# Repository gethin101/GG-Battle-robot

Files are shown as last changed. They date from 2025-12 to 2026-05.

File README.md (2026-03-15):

# Gethin's Custom BATTLE ROBOT
**This is my custom Robot Wars inspired battle robot with a servo-driven axe weapon, wireless radio frequency remote control, LCD display, RGB lights, and audio sound effects. My robot is controlled by a custom PCB RF remote using a Raspberry Pi Pico H microcontroller running CircuitPython and the chassis and axe will be 3D printed in PLA.**

It runs on a Raspberry pi pico H, TT motors, L298N motor drivers, and a servo motor. It is controlled by a 433mhz radio frequency remote, another Raspberry pi pico H, a joystick module and extra control buttons. The 2 main axe weapons and chassis will be 3d printed in PLA.

I am also using a 1.8" SPI LCD Display for the robot to display information on the front of the robot and SK6812 MINI-E RGB leds for the back of the robot. These will both be powered by being plugged into the breadboard in the robot using the pins and jumper wires.

Also I have sound effects for my robot. I will do this through a PAM8302 amplifier board and 8Ω 2W speaker. The amplifier board will go into the breadboard & the speaker will plug directly into the PAM8302.

**It is powered by AA batteries, the actual robot will be connected using a breadboard & jumper wires, but I wanted to create a custom PCB for my remote. I designed the PCB in KiCad, also with female sockets so I can remove modules from the remote.**

**Note:** I had to connect the grounds on either side together so they have the same voltage reference point.

My weapon system consists of a servo motor embedded on the underside of the top half of the chassis that will swing the PLA axe weapon down to hit, and back up to rest on the slanted design of the robot.

---

## Inspiration
I wanted to make this project to help me learn CAD design through Fusion 360, PCB design in KiCad and get me into the world of electronics and embedded systems.
I designed my robot with inspiration from Thor in Robot Wars with the axe weapon idea and Apollo with the general shape and aesthetics

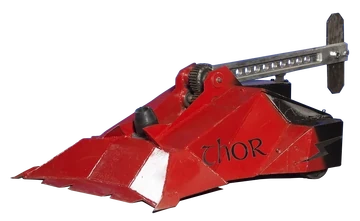
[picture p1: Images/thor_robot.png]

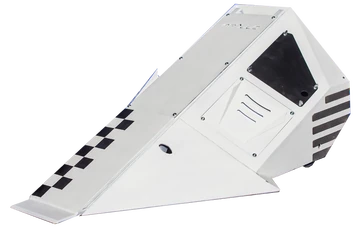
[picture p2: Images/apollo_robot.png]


---

## Control

I control my robot through the use of the PCB remote. There is a joystick module that with the use of the RF transmitter, will control the TT motors on the robot and therefore the movement of the wheels. 

I have also added a button on the remote to control the servo motor that moves the PLA axe weapon and also a few buttons that play sound effects and display custom data on the display.

---

## **Remote PCB:**

**Solder:**
- Battery wires to copper pad
- Pico through hole
- Buttons

**Headers:**
- RF module
- Joystick
- Boost converter

Remote PCB design:

**This was my first PCB design before I made it in KiCad**

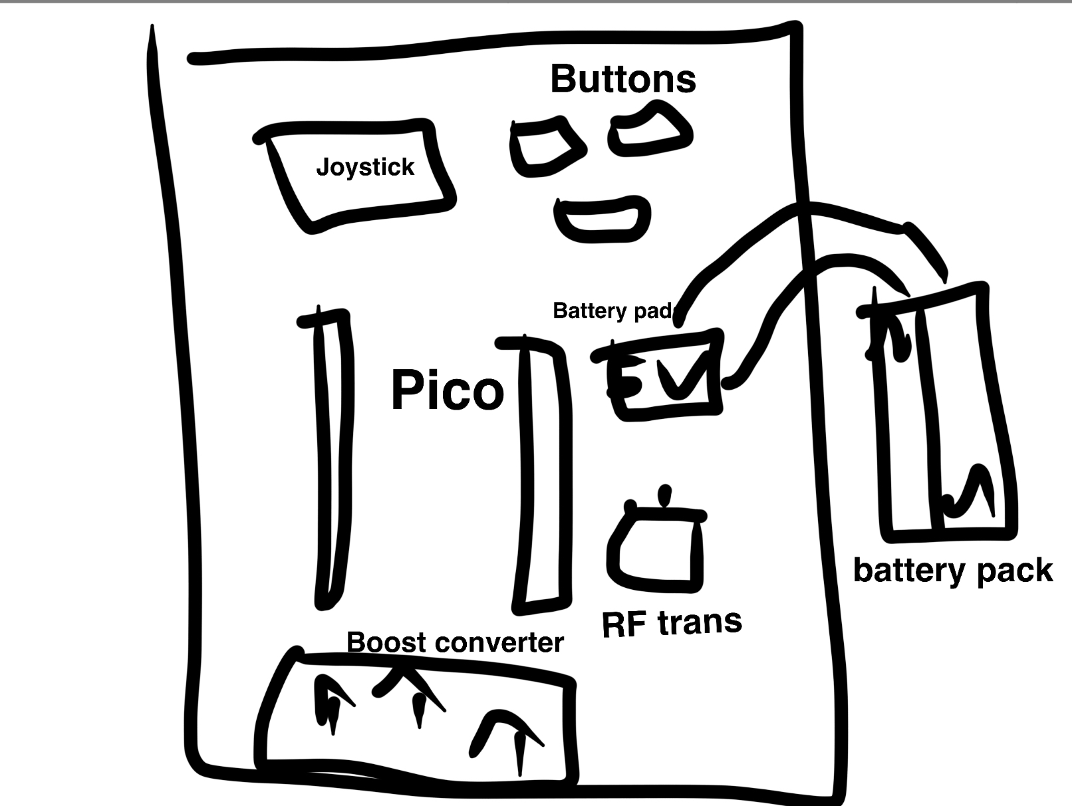
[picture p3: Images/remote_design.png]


I then designed my remote PCB in KiCad with the schematic below showing how all the components are connected:

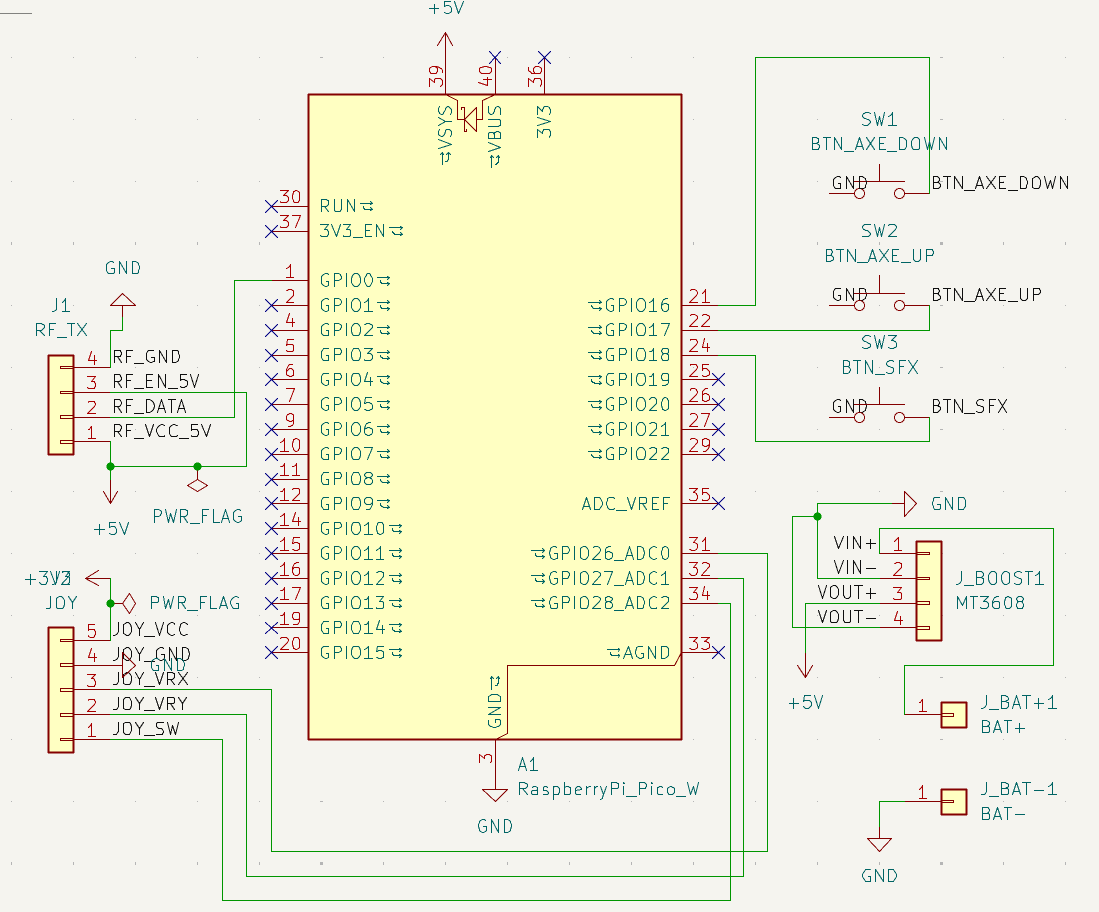
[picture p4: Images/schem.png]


**PCB design process:**

I designed my remote PCB in KiCad. I made through-hole pins for the pico where I will have the choice to either solder on female headers which will allow easy removal of the pico for the remote or to directly solder them on. 
This took some time to design as I wasn't sure on which approach would better fit my project, so I left it for my decision when I get the parts.

Next, I added 3 small buttons that I will solder straight onto the PCB. These will be used as control buttons for the robot where I will program them to sent certains signals to the robot, for example to move the axe head up or down with the servo motor, or to carry out pre-programmed movement plans with the TT motors and wheels.

I added two copper pads for the battery+ and battery- to my PCB to power the remote and I ended up decising to put these on the back side of the PCB so it leaves more space on the front and so I can more easily secure the battery pack on the rear side of the remote, with plently of space to move it around before deciding the final position.

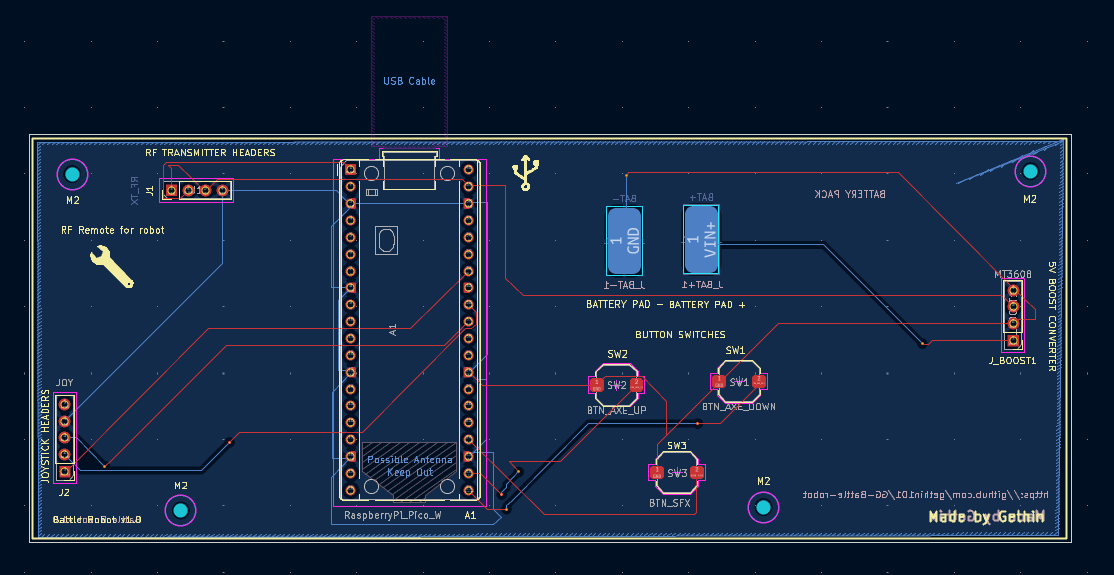
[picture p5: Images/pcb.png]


I added holes in my PCB where I will solder on female header pins for the radio frequency transmitter device so it can be easily removed if I come across any issues. I repeated this process on different parts of the remote for the joystick device and 5V boost converter to allow for efficient and easy assembly once I'm ready to build my robot. I first went for through-hole pins in my original design but altered it to have header pins as it will be easier to assemble and tinker with.

Next, I added some silkscreen details onto my PCB such as my name, GitHub repo link and a small mechanical logo. This added a bit more personality to my remote and will allow for it to be easier to distinguish from other robots (ik this is only the remote and will most likely be covered later on, but it was fun to mess about with)

I learnt how to add drill holes on the corners of my PCB so it has the option to be secured into a case and therefore will be more comfortable to use with nothing moving about. Furthermore, I also learnt how to make a copper GND pour which I have found out reduces noise on the PCB and allowed me to have better accessibility to the GND on the remote when I was designing and wiring it in KiCad.

I am happy with my remote PCB and I ran the ERC and DRC checkers a few times, fixed all the issues and now it comes up with no errors when I run them.

The KiCad project files & gerber.zip are both in **PCB/** and the PCB cart screenshot from JLCPCB is below

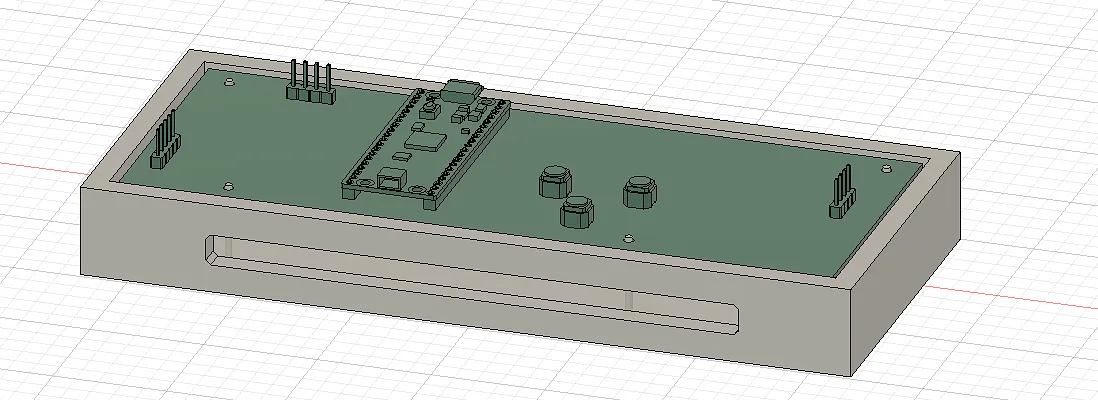
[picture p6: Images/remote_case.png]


---

## Cart Screenshots

**Here are the cart screenshots for all of my components. I have logged the prices exactly, but there are some discounts and sales on atm that are ending soon so it may end up costing a bit more.**

<details>
<summary>Click to see cart screenshots</summary>
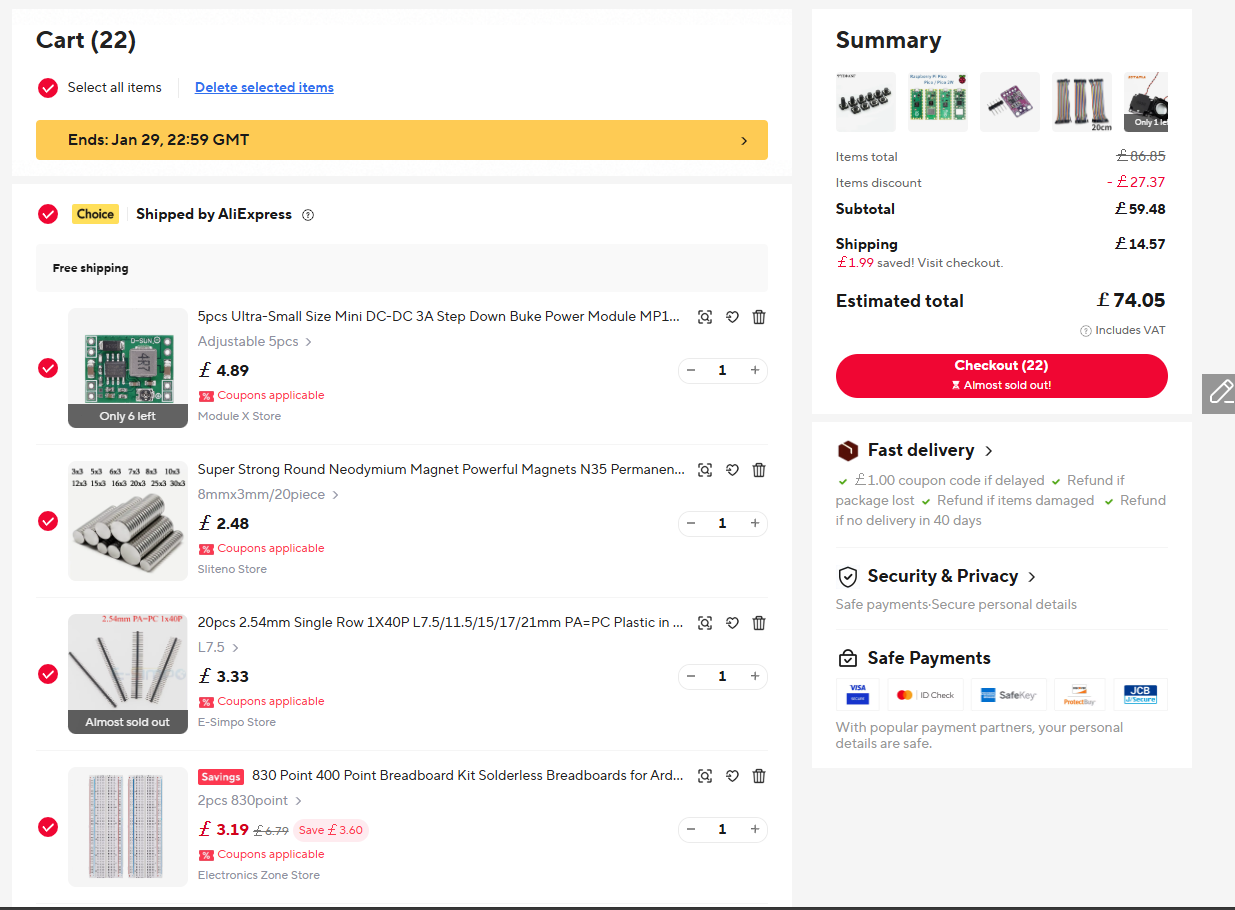
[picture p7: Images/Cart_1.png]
cart screenshot


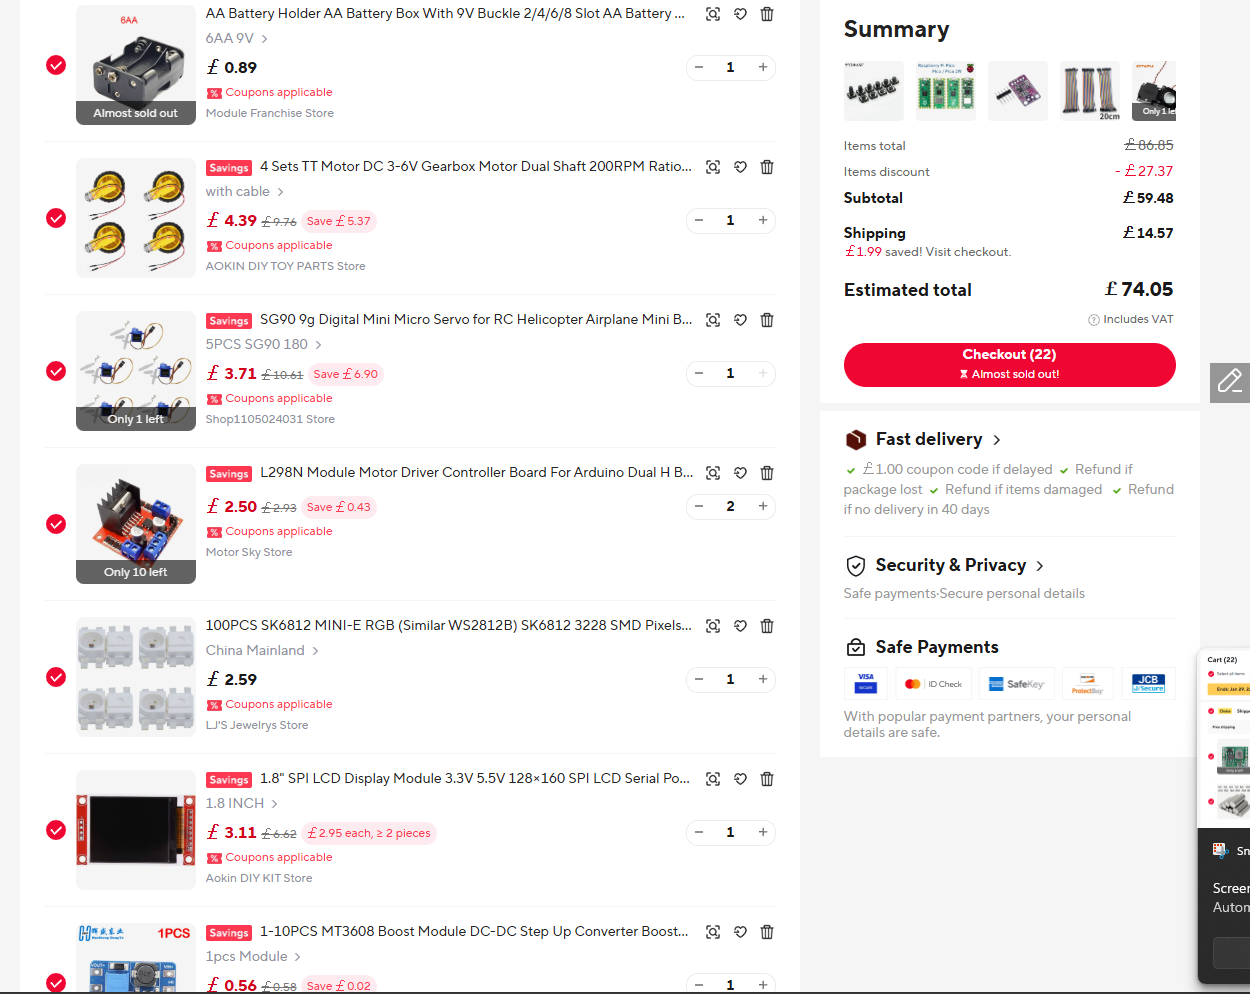
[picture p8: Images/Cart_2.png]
cart screenshot


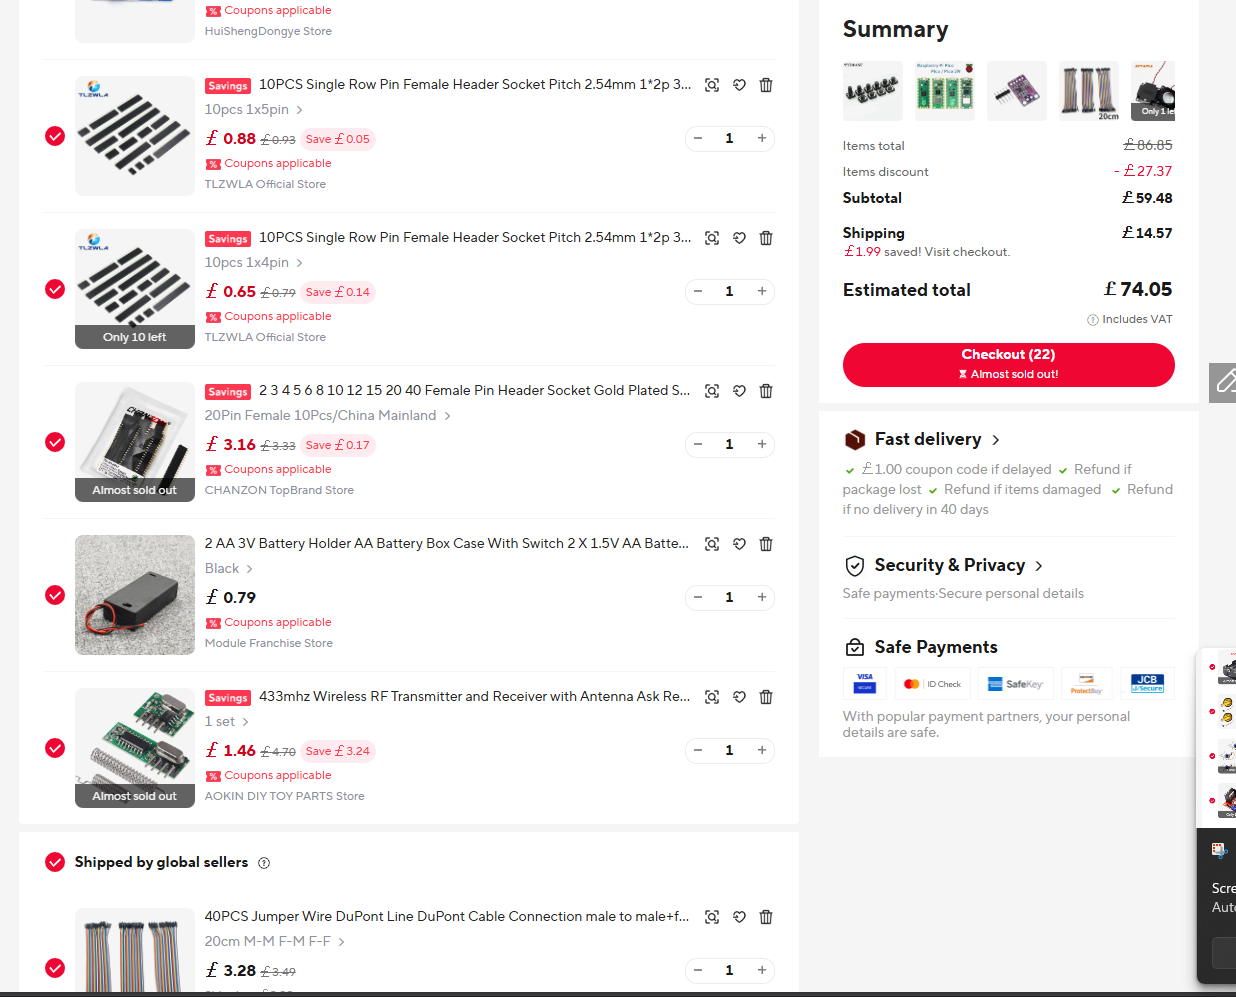
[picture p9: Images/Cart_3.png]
cart screenshot


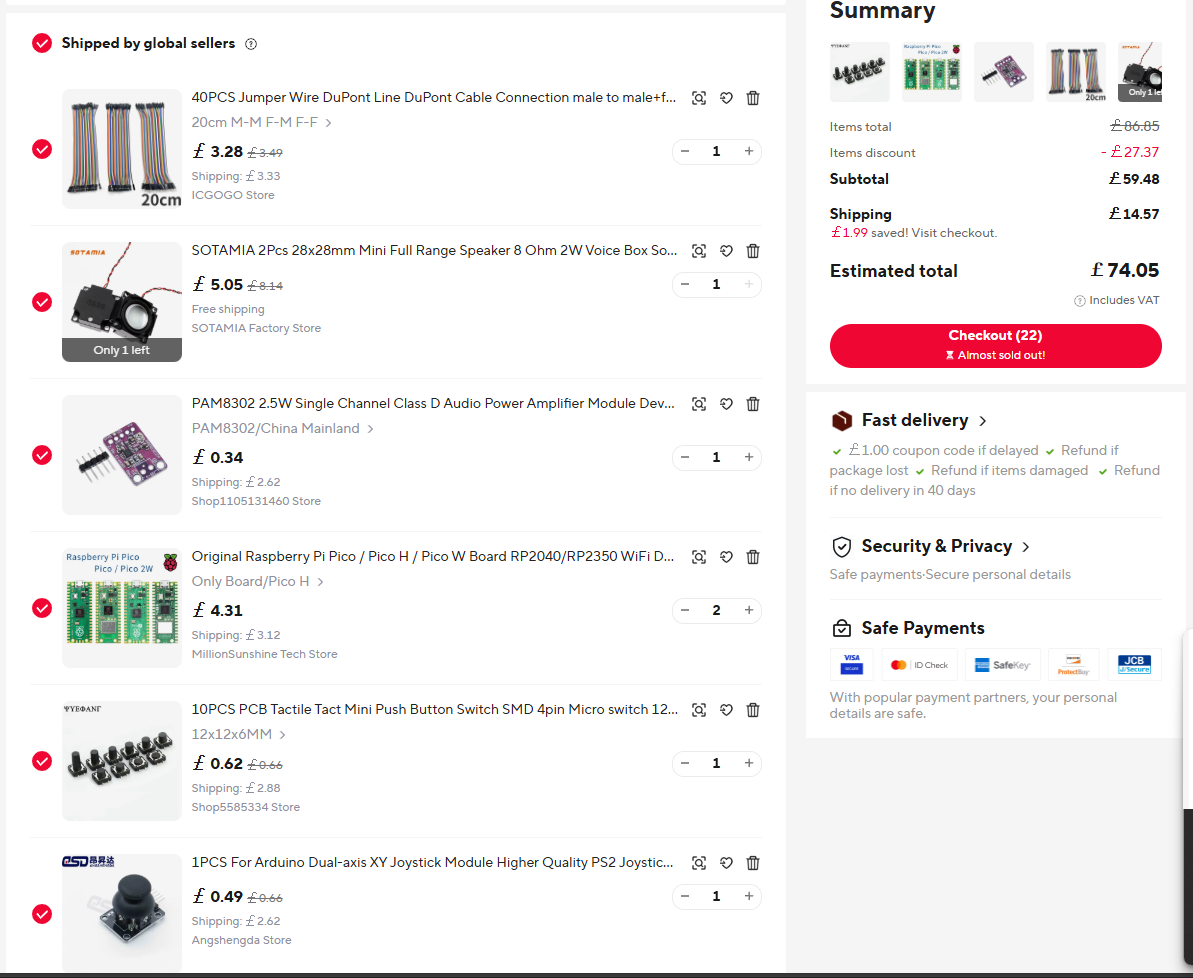
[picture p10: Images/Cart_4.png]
cart screenshot


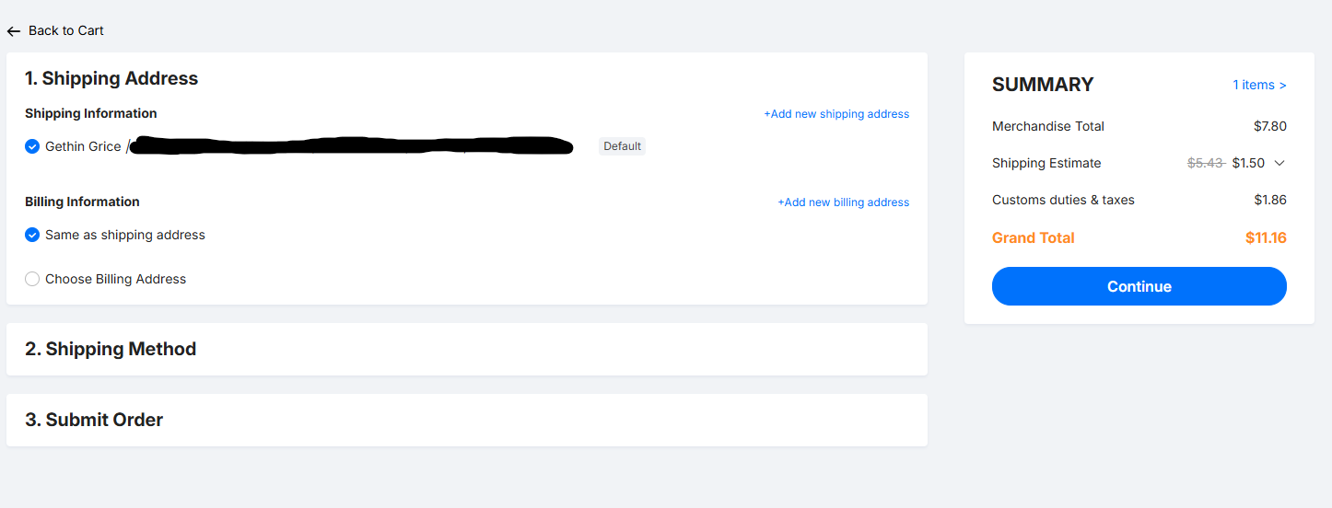
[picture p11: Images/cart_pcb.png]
cart screenshot

</details>

---

## Components

Here are the lists of components for my robot. I have also made a [full BOM](BOM.md)
with links to all the parts.

**List of components for remote:**

- Raspberry pi pico H
- Joystick module
- 433 MHz transmitter
- 2xAA Battery pack
- Custom PCB for joystick, transmitter, microcontroller, battery input & boost converter
- A few buttons for display, audio & specific movement plans
- Female sockets for component removal
- 5V boost converter

**List of components for robot:**

- Raspberry pi pico H
- 1.8" SPI LCD Display
- SK6812 MINI-E RGBs
- PAM8302 amplifier board
- 8Ω 2W speaker
- 433 MHz receiver
- 2x L298N motor drivers
- 4x TT motors (raw voltage from L298Ns)
- Servo motor
- 6xAA battery pack
- Breadboard
- Jumper wires for wiring
- PLA axe
- 3D printed chassis
- 5V buck converter
- Magnets for top & bottom chassis connection

**My project should cost around $104 so should be tier 2**

---
This was my first hand sketch of the component positioning in my robot but obviously I've changed bits of it

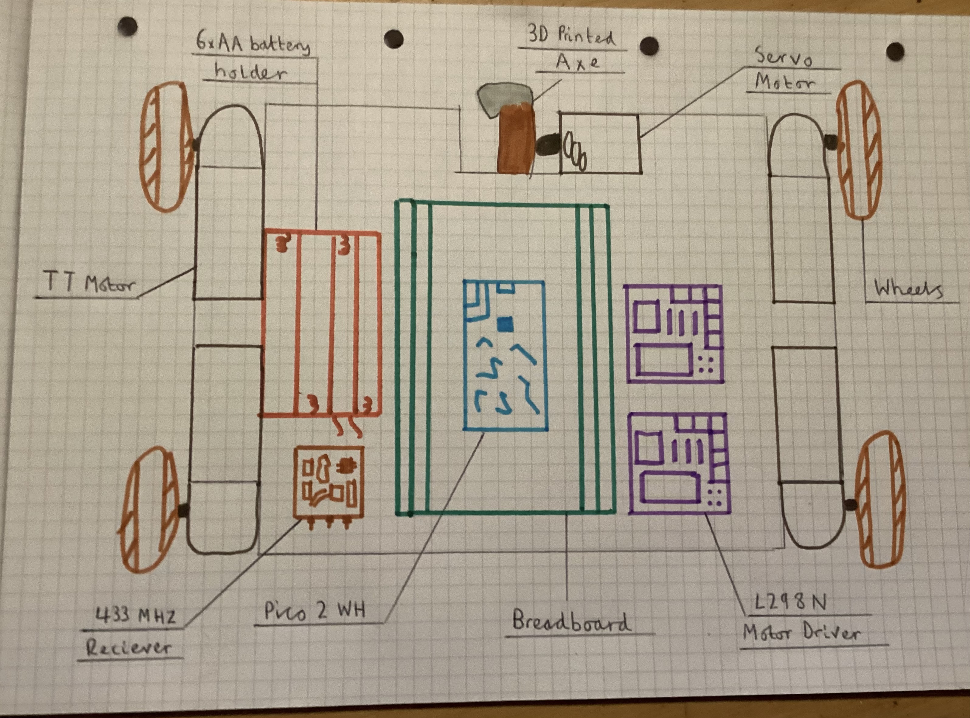
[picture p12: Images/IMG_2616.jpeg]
original wiring diagram


This is a (bit messy) wiring diagram for the robot breadboard system

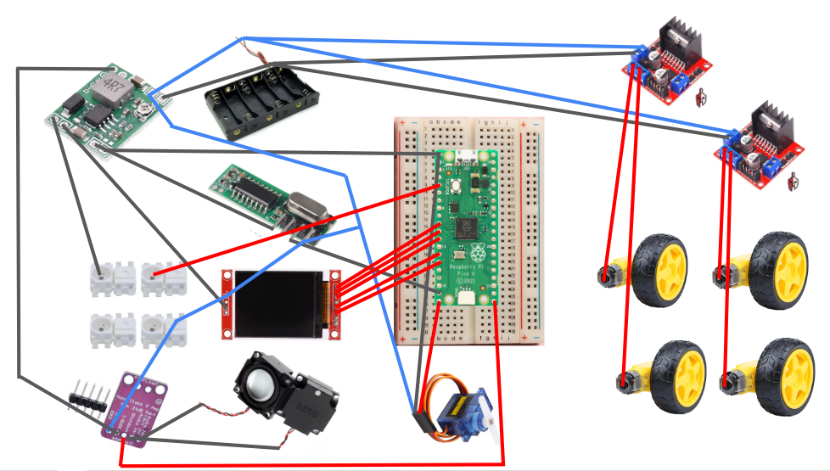
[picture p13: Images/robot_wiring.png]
wiring diagram robot


---

First 3D fusion model of robot chassis:

I originally designed it like this with 2 axe weapons and patterns but have changed to the version below instead.

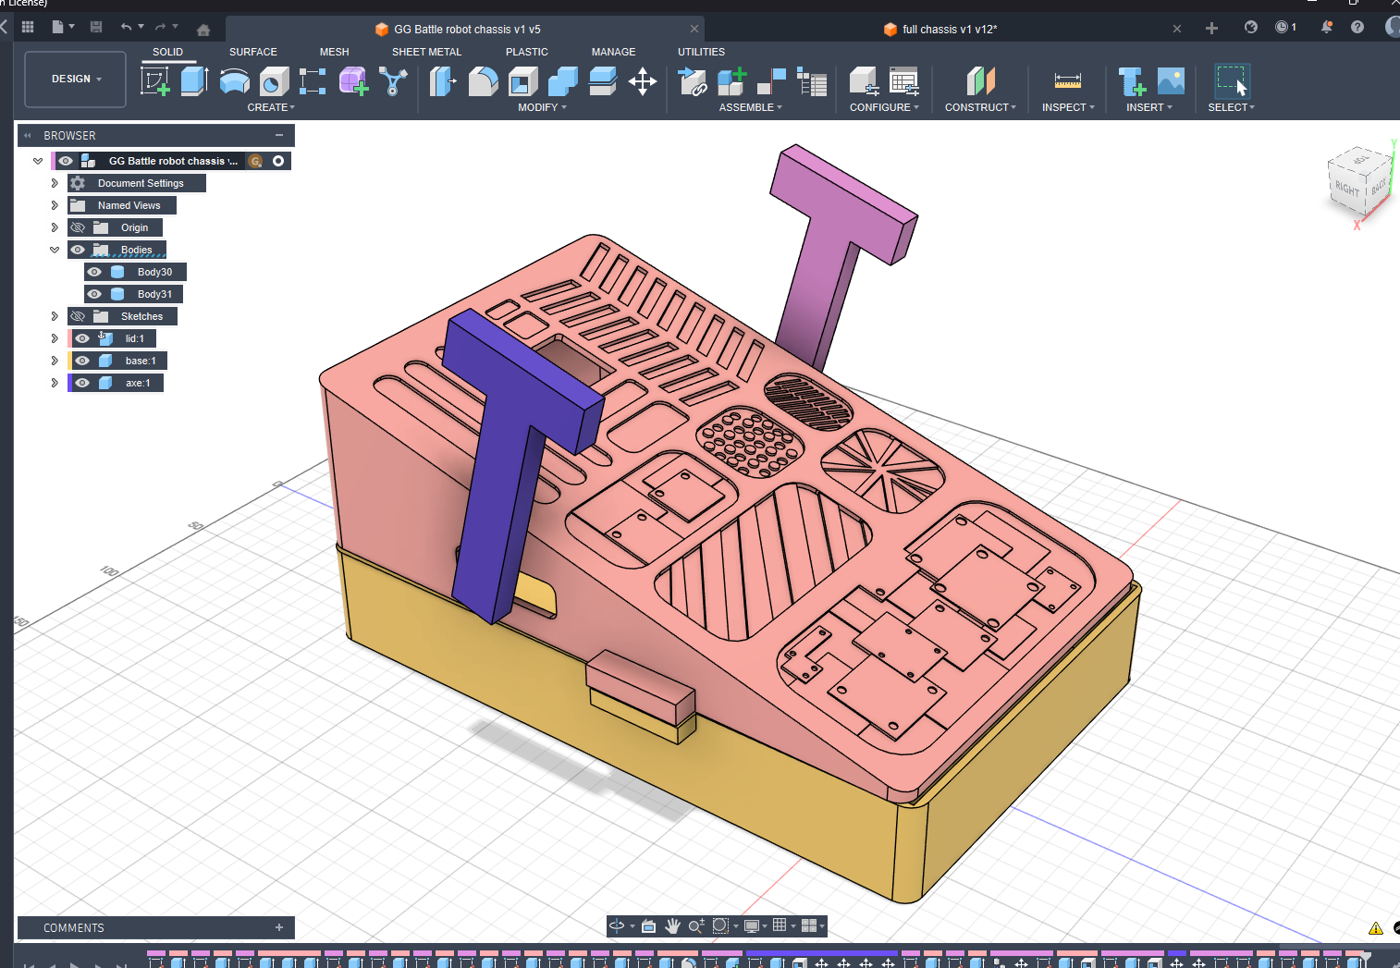
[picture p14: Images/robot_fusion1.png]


This version is the final concept for my robot chassis

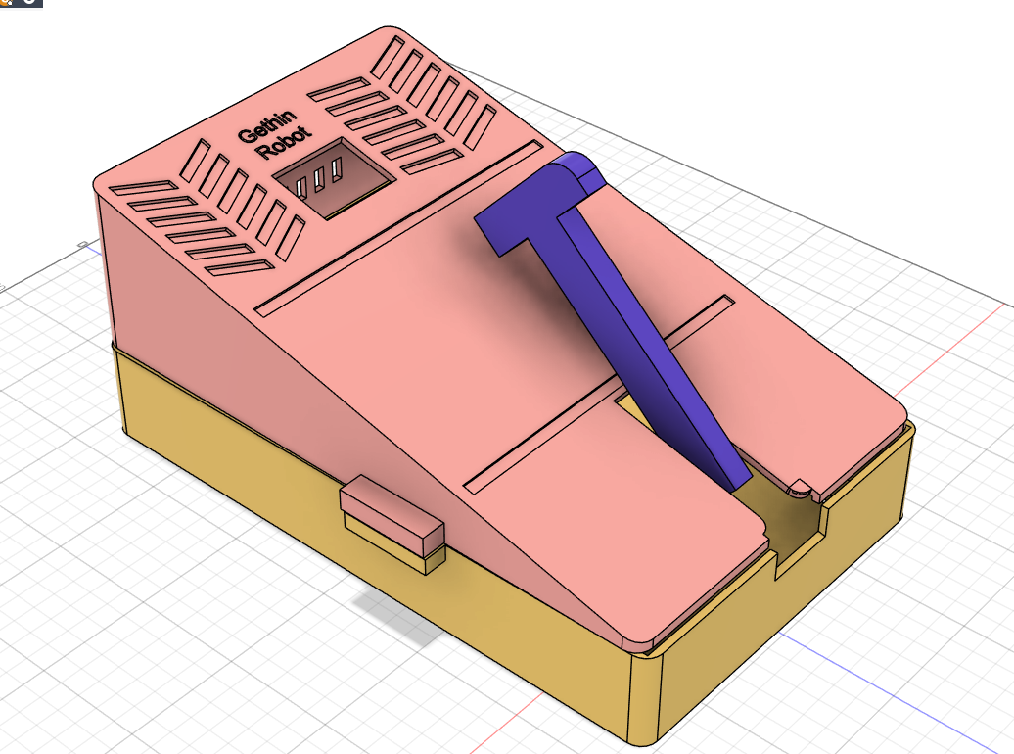
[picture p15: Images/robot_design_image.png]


Rendered robot with textures applied & motors & wheels components

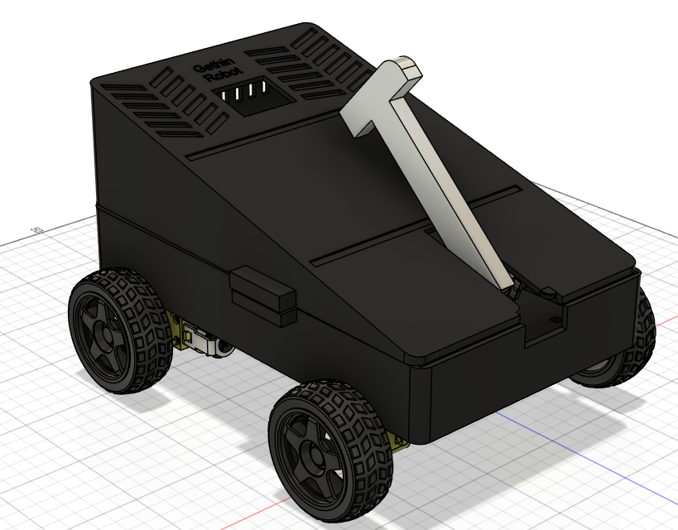
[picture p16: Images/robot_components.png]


Showing servo motor setup with axe and TT motors

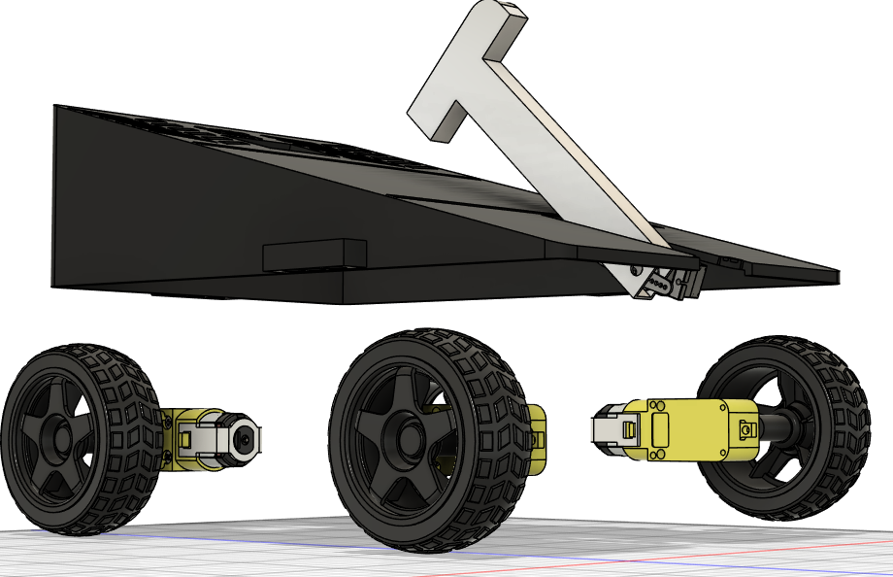
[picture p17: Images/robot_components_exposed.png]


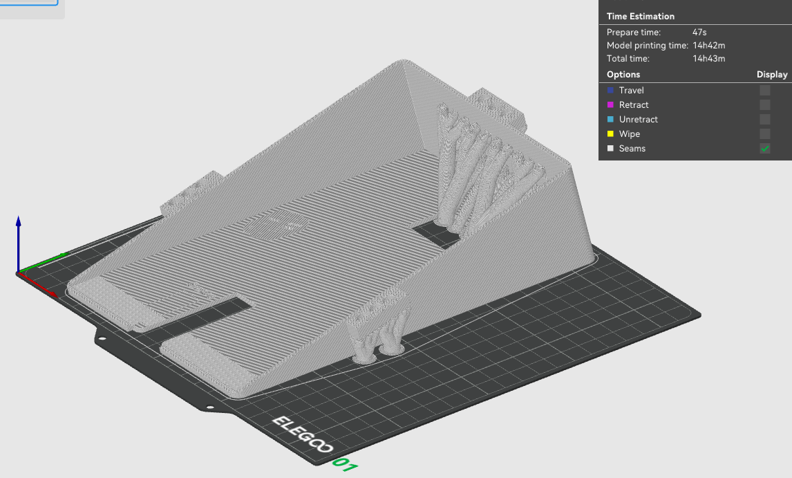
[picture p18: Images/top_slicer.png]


Base bottom of the robot without top half of the chassis

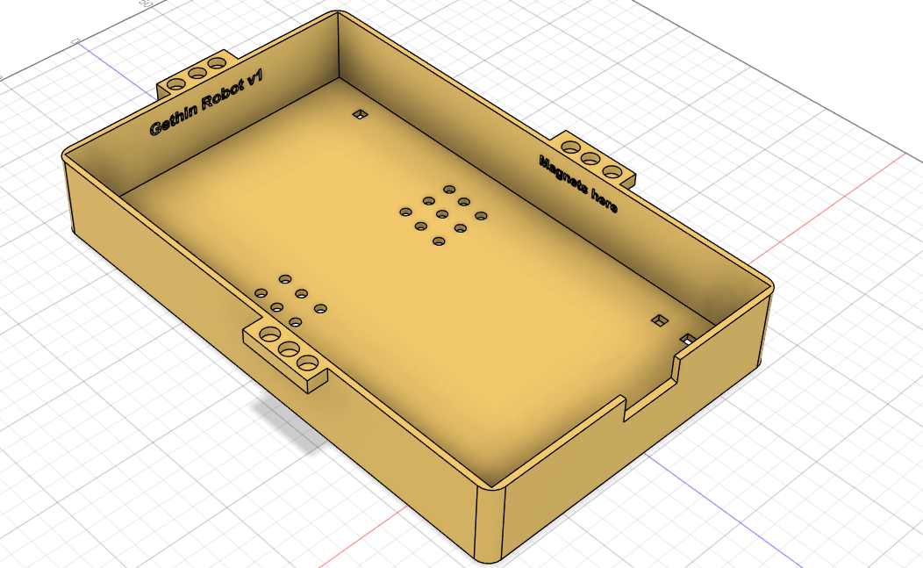
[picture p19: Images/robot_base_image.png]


---
# BOM

**Please note that I am requesting $100 and I will pay for the rest myself**

See [BOM](/BOM.csv)

---
**I will make different iterations and designs for the chassis another time but this is my first design for blueprint**

---

## CircuitPython firmware

- I will need to flash [CircuitPython](/Firmware/adafruit-circuitpython-raspberry_pi_pico2-en_GB-10.1.3.uf2) onto my picos
- Install circuitpython libraries .mpys
- Upload the different [code.pys](Firmware/) to my picos
- Test the firmwares are working

# Blueprint requirements

- [✅] A short description of what your project is  
- [✅] A couple of sentences on how to use your project  
- [✅] A couple of sentences on why you made the project  

- [✅ ] Screenshot of a full 3D model of your project  
- [✅ ] Screenshot of your PCB (if applicable)  
- [✅ ] Wiring diagram (if any wiring is not on a PCB)  
- [✅] Bill of Materials (BOM) in table format at the end of the README, with links [BOM](/BOM.csv)

- [✅] Fully original, customized design (not a direct copy of any guide)  
- [✅] Complete CAD assembly including all components (electronics included)  
- [✅] Firmware present (even if untested)  
- [✅] Design sanity‑checked with someone else  approved by [@LoganPeterson](https://hackclub.enterprise.slack.com/team/U079WLY0HLY)

- [✅] BOM in CSV format in the root directory, with links
- [✅] PCB source files (.kicad_pro, .kicad_sch, gerbers.zip, etc.) if applicable  
- [✅] A .STEP file of the full 3D CAD model including electronics  
- [✅] Source CAD files (.f3d, .FCStd, etc., or OnShape public link in README)  
- [✅] All other project files included (firmware, libraries, references, etc.)  
- [✅] Repository organized into readable, logical folders  

> ⚠️ **Important:** Missing a complete .STEP file with all electronics and CAD will result in project rejection. ✅

## 📝 License
This project is open-source under the MIT License and was designed & built during Hackclub Blueprint 2025-26 by [@gethin101](https://github.com/gethin101)

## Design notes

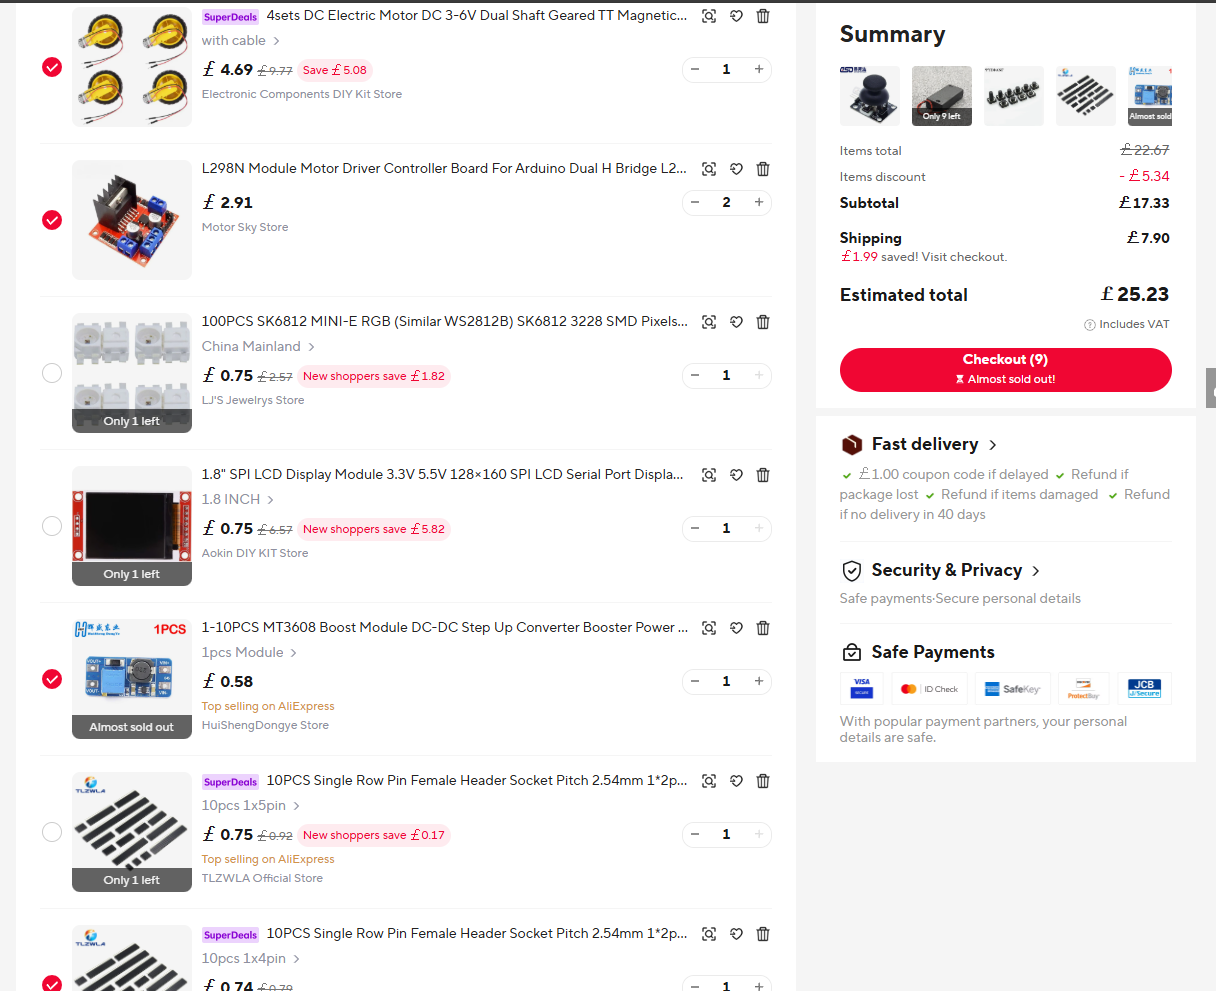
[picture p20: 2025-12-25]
Images/Screenshot 2025-12-25 172446.png

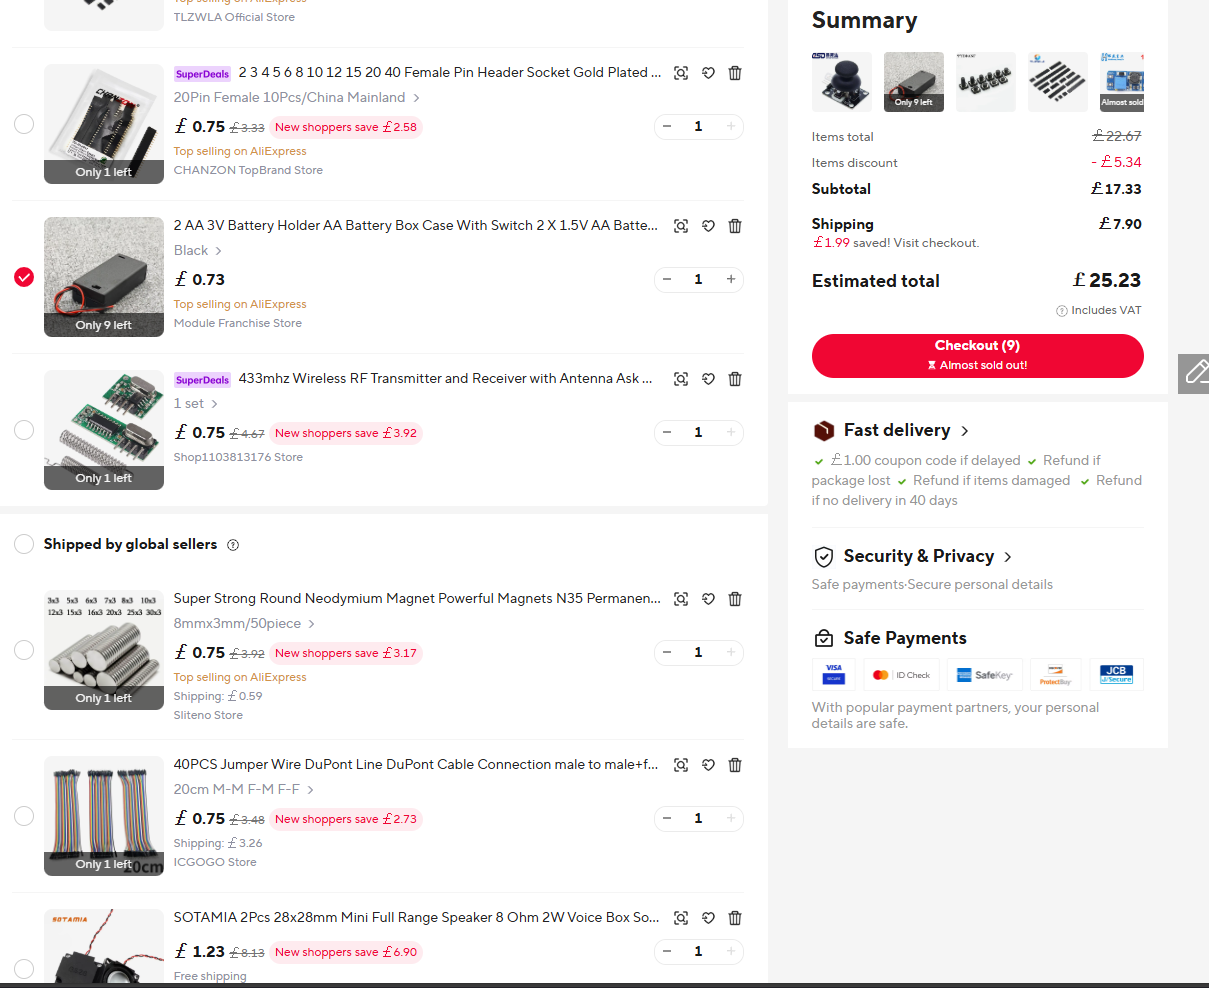
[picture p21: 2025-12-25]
Images/Screenshot 2025-12-25 172452.png

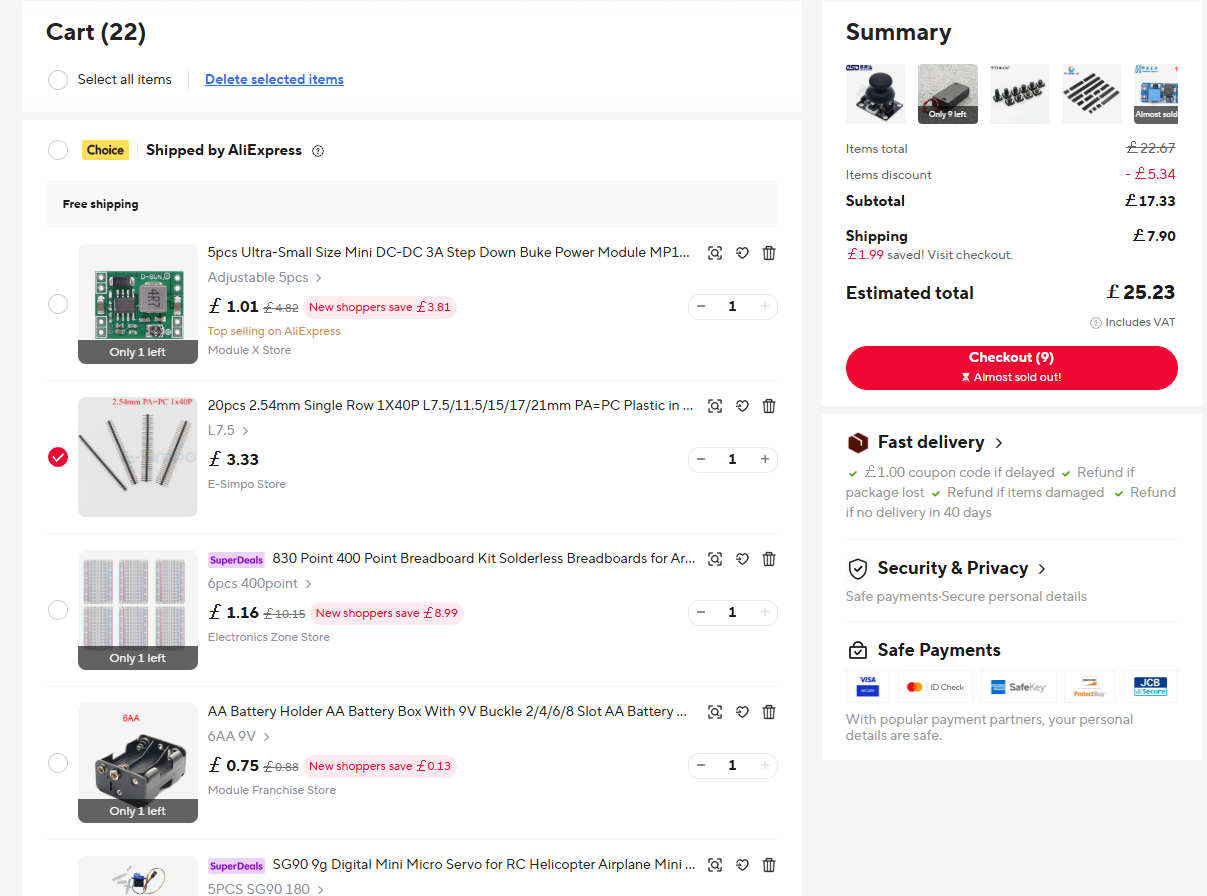
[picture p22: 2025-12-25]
Images/Screenshot 2025-12-25 172439.png

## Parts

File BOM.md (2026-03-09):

## Remote Components

**Totals £82.32 or $112.29** with shipping factored in **(OLD)**

**Now totals £78.20 or $104.30**

| Name | Use | Link | Price | US |
|---|-----|---|---|----|
| Joystick module | Used to control the robot movement | [link](https://www.aliexpress.com/item/1005010212257095.html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) | £0.49 | $0.67 |
| 433 MHz transmitter & receiver | Sends control signals to robot | [link](https://www.aliexpress.com/item/1005007239689710.html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) | £0.76 | £1.04 |
| 2×AA battery pack | Powers the remote | [link](https://www.aliexpress.com/item/1005001750984235.html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) | £0.76 | $1.04 |
| Custom PCB | Will have the joystick, transmitter, Pico & boost converter | [Custom](https://jlcpcb.com/) | £8.28 | $11.29 |
| Buttons | Used for weapon control (SMD) | [link](https://www.aliexpress.com/item/1005005279088080.html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) | £0.62 | $0.85 |
| Sockets 1 | Allow me to remove pico (20 pin) | [link](https://www.aliexpress.com/item/1005003610333849.html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) | £0.76 | $1.04 |
| Sockets 2 | (1x4 pin) & (1x5 pin)| [link](https://www.aliexpress.com/item/4001198421663.html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) | £1.41 | $1.92 |
| 5V boost converter | Steps up 3V from AA pack to 5V | [link](https://www.aliexpress.com/item/1005006361814667.html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) | £0.56 | $0.76 |

---

## Robot Components

| Name | Use | Link | Price | US |
|---|-----|---|---|----|
| Pi Pico welding | Microcontroller for robot | [1](https://www.aliexpress.com/item/1005003740742365.html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) [2](https://www.aliexpress.com/item/1005008948799927.html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) | £1.54 | $2.05 |
| 1.8" SPI LCD Display  | Screen for displaying info | [link](https://www.aliexpress.com/item/1005008721040252.html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) | £3.11 | $4.24 |
| SK6812 MINI-E RGB | LED lights for my robot | [link](https://www.aliexpress.com/item/1005005186515165.html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) | £0.76 | $1.04 |
| PAM8302 amplifier | Amplifier for the speaker on the robot | [link](https://www.aliexpress.com/item/1005010400102160.html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) | £0.34 | $0.46 |
| 8Ω 2W round speaker | Speaker to play sound effects on the robot | [link](https://www.aliexpress.com/item/1005007348631655.html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) | £1.62 | $2.21 |
| 2× L298N motor drivers | For the TT motors | [link](https://www.aliexpress.com/item/1005008277888797.html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) | £5.00 | $6.82 |
| 4× TT motors | Motors for wheels | [link](https://www.aliexpress.com/item/1005007805394977.html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) | £4.39 | $5.99 |
| MG996 servo (360) | Moves the PLA axe weapon | [link](https://www.aliexpress.com/item/1005009497648073.html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,scm-url:1007.23125.137358.0,pvid:1bee5fa3-bfe9-43bd-ad29-3ee96f4c97cf,tpp_buckets:668%232846%238111%231996&pdp_ext_f=%7B%22order%22%3A%221970%22%2C%22eval%22%3A%221%22%2C%22sceneId%22%3A%2213125%22%2C%22fromPage%22%3A%22recommend%22%7D&pdp_npi=6%40dis%21GBP%213.08%210.77%21%21%2127.56%216.92%21%402103868817730429325465970e6369%2112000049284144091%21rec%21UK%21%21ABXZ%211%210%21n_tag%3A-29910%3Bd%3Ac7b67d0a%3Bm03_new_user%3A-29895%3BpisId%3A5000000197842857&spm=a2g0o.store_pc_home.smartJustForYou_2006930920852.1005009497648073) | £0.76 | $1.04 |
| 6×AA battery pack | Powers motors and components | [link](https://www.aliexpress.com/item/1005004798582970.html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) | £0.76 | $1.04 |
| Breadboard | Where everything will be connected | [link](https://www.aliexpress.com/item/1005008787753880.html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) | £0.76 | $1.04 |
| Male header pins | (L7.5) for boost converter | [link](https://www.aliexpress.com/item/1005008747214913.html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) | £0.76 | $1.04 |
| Jumper wires | Connect Pico, drivers, servo & rf receiver (20cm) | [link](https://www.aliexpress.com/item/1005006616309305.html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) | £3.28 | $4.47 |
| Magnets to connect lid and main chassis | 8mm x 3mm option - need holes in chassis| [link](https://www.aliexpress.com/item/1005010051950544.html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) | £0.76 | $1.04 |
| 5V buck converter | Steps down 9V battery to 5V | [link](https://www.aliexpress.com/item/1005005305772411.html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) | £4.89 | $6.67 |

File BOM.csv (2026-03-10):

Name | Use | Link | Price | US
Joystick module | Used to control the robot movement | https://www.aliexpress.com/item/1005010212257095.html | £0.49 | $0.67
433 MHz transmitter & receiver | Sends control signals to robot | https://www.aliexpress.com/item/1005007239689710.html | £0.76 | £1.04
2×AA battery pack | Powers the remote | https://www.aliexpress.com/item/1005001750984235.html | £0.76 | $1.04
Custom PCB | Will have the joystick - transmitter - Pico & boost converter | https://jlcpcb.com/ | £8.28 | $11.29
Buttons | Used for weapon control (SMD) | https://www.aliexpress.com/item/1005005279088080.html | £0.62 | $0.85
Sockets 1 | Allow me to remove pico (20 pin) | https://www.aliexpress.com/item/1005003610333849.html | £0.76 | $1.04
Sockets 2 | (1x4 pin) & (1x5 pin) | https://www.aliexpress.com/item/4001198421663.html | £1.41 | $1.92
5V boost converter | Steps up 3V from AA pack to 5V | https://www.aliexpress.com/item/1005006361814667.html | £0.56 | $0.76
Pi Pico welding | Microcontroller for robot | https://www.aliexpress.com/item/1005003740742365.html | https://www.aliexpress.com/item/1005008948799927.html | £1.54 | $2.05
1.8' SPI LCD Display | Screen for displaying info | https://www.aliexpress.com/item/1005008721040252.html | £3.11 | $4.24
SK6812 MINI-E RGB | LED lights for my robot | https://www.aliexpress.com/item/1005005186515165.html | £0.76 | $1.04
PAM8302 amplifier | Amplifier for the speaker on the robot | https://www.aliexpress.com/item/1005010400102160.html | £0.34 | $0.46
8Ω 2W round speaker | Speaker to play sound effects on the robot | https://www.aliexpress.com/item/1005007348631655.html | £1.62 | $2.21
2× L298N motor drivers | For the TT motors | https://www.aliexpress.com/item/1005008277888797.html | £5.00 | $6.82
4× TT motors | Motors for wheels | https://www.aliexpress.com/item/1005007805394977.html | £4.39 | $5.99
MG996 servo (360) | Moves the PLA axe weapon | https://www.aliexpress.com/item/1005009497648073.html | £0.76 | $1.04
6×AA battery pack | Powers motors and components | https://www.aliexpress.com/item/1005004798582970.html | £0.76 | $1.04
Breadboard | Where everything will be connected | https://www.aliexpress.com/item/1005008787753880.html | £0.76 | $1.04
Male header pins | (L7.5) for boost converter | https://www.aliexpress.com/item/1005008747214913.html | £0.76 | $1.04
Jumper wires | Connect Pico - drivers - servo & rf receiver (20cm) | https://www.aliexpress.com/item/1005006616309305.html | £3.28 | $4.47
Magnets to connect lid and main chassis | 8mm x 3mm option - need holes in chassis | https://www.aliexpress.com/item/1005010051950544.html | £0.76 | $1.04
5V buck converter | Steps down 9V battery to 5V | https://www.aliexpress.com/item/1005005305772411.html | £4.89 | $6.67

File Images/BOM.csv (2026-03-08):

Name | Use | Link | Price | US
Joystick module | Used to control the robot movement | https://www.aliexpress.com/item/1005010212257095.html?curPageLogUid=QsdQjQrewpMZ | £0.49 | $0.67
433 MHz transmitter & receiver | Sends control signals to robot | https://www.aliexpress.com/item/1005007239689710.html | £0.76 | £1.04
2×AA battery pack | Powers the remote | https://www.aliexpress.com/item/1005001750984235.html?curPageLogUid=GHC6WV3RikNM | £0.76 | $1.04
Custom PCB | Will have the joystick, transmitter, Pico & boost converter | https://jlcpcb.com/ | £8.28 | $11.29
Buttons | Used for weapon control (SMD) | https://www.aliexpress.com/item/1005005279088080.html?curPageLogUid=MsjHNI0p6bdL | £0.62 | $0.85
Sockets 1 | Allow me to remove pico (20 pin) | https://www.aliexpress.com/item/1005003610333849.html?curPageLogUid=EKxEHOcWPDT9 | £0.76 | $1.04
Sockets 2 | (1x4 pin) & (1x5 pin) | https://www.aliexpress.com/item/4001198421663.html?curPageLogUid=nHKqqtqvQU2q | £1.41 | $1.92
5V boost converter | Steps up 3V from AA pack to 5V | https://www.aliexpress.com/item/1005006361814667.html?curPageLogUid=MEA3qFzpW1eG | £0.56 | $0.76
Raspberry Pi Pico H x2 | Microcontroller for robot | https://www.aliexpress.com/item/1005009646610678.html?mp=1 | £8.62 | $11.76
1.8\ SPI LCD Display | Screen for displaying info | https://www.aliexpress.com/item/1005008721040252.html?spm=a2g0o.productlist.main.25.501f3237yQO86V | £3.11 | $4.24
SK6812 MINI-E RGB | LED lights for my robot | https://www.aliexpress.com/item/1005005186515165.html?spm=a2g0o.productlist.main.2.35706ab6e3eama | £0.76 | $1.04
PAM8302 amplifier | Amplifier for the speaker on the robot | https://www.aliexpress.com/item/1005010400102160.html?spm=a2g0o.productlist.main.12.34a1z7daz7daAy | £0.34 | $0.46
8Ω 2W round speaker | Speaker to play sound effects on the robot | https://www.aliexpress.com/item/1005007348631655.html?spm=a2g0o.productlist.main.3.27001d2ePw3tCq | £1.62 | $2.21
2× L298N motor drivers | For the TT motors | https://www.aliexpress.com/item/1005008277888797.html?spm=a2g0o.productlist.main.4.5bd26d2aLbRqB5 | £5.00 | $6.82
4× TT motors | Motors for wheels | https://www.aliexpress.com/item/1005007805394977.html?spm=a2g0o.productlist.main.25.cd2cdJDAdJDAMM | £4.39 | $5.99
Servo motor (180) | Moves the PLA axe weapon | https://www.aliexpress.com/item/1005010072923650.html?spm=a2g0o.productlist.main.1.3c1053ffaEhkTt | £0.76 | $1.04
6×AA battery pack | Powers motors and components | https://www.aliexpress.com/item/1005004798582970.html?spm=a2g0o.productlist.main.15.77f69qL39qL3nQ | £0.76 | $1.04
Breadboard | Where everything will be connected | https://www.aliexpress.com/item/1005008787753880.html?spm=a2g0o.productlist.main.1.78b556f3I1CHsN | £0.76 | $1.04
Male header pins | (L7.5) for boost converter | https://www.aliexpress.com/item/1005008747214913.html?spm=a2g0o.productlist.main.6.7b8d2e28Eacau3 | £0.76 | $1.04
Jumper wires | Connect Pico, drivers, servo & rf receiver (20cm) | https://www.aliexpress.com/item/1005006616309305.html?spm=a2g0o.productlist.main.20.1d7253e8Gd50w1 | £3.28 | $4.47
Magnets to connect lid and main chassis | 8mm x 3mm option - need holes in chassis | https://www.aliexpress.com/item/1005010051950544.html?spm=a2g0o.productlist.main.1.4847Z0xSZ0xSH4 | £0.76 | $1.04
5V buck converter | Steps down 9V battery to 5V | https://www.aliexpress.com/item/1005005305772411.html?spm=a2g0o.productlist.main.18.1069fc01oftGiw | £4.89 | $6.67
Total | All from aliexpress except from PCB | N/A | £82.32 | $112.29

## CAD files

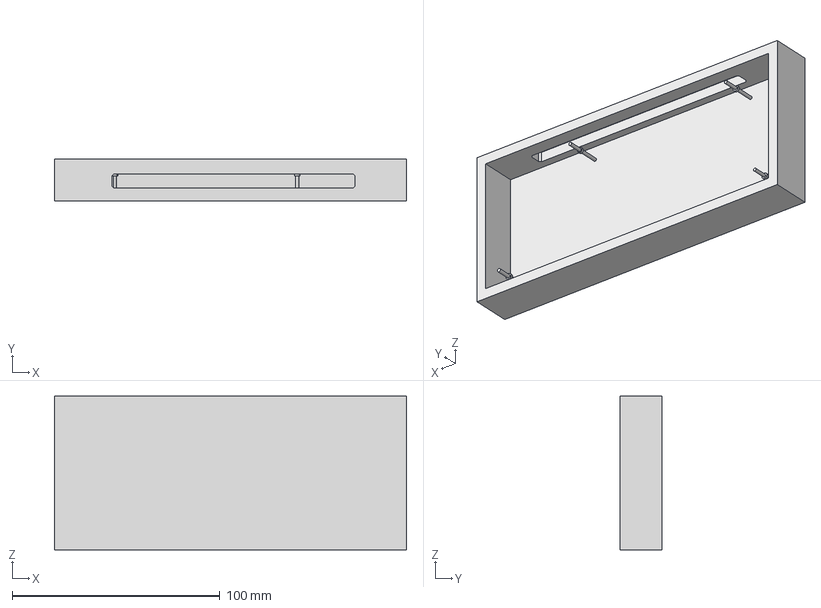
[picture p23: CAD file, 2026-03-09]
3D Models/robot remote CASE.step
169.4 x 20.0 x 73.9 mm

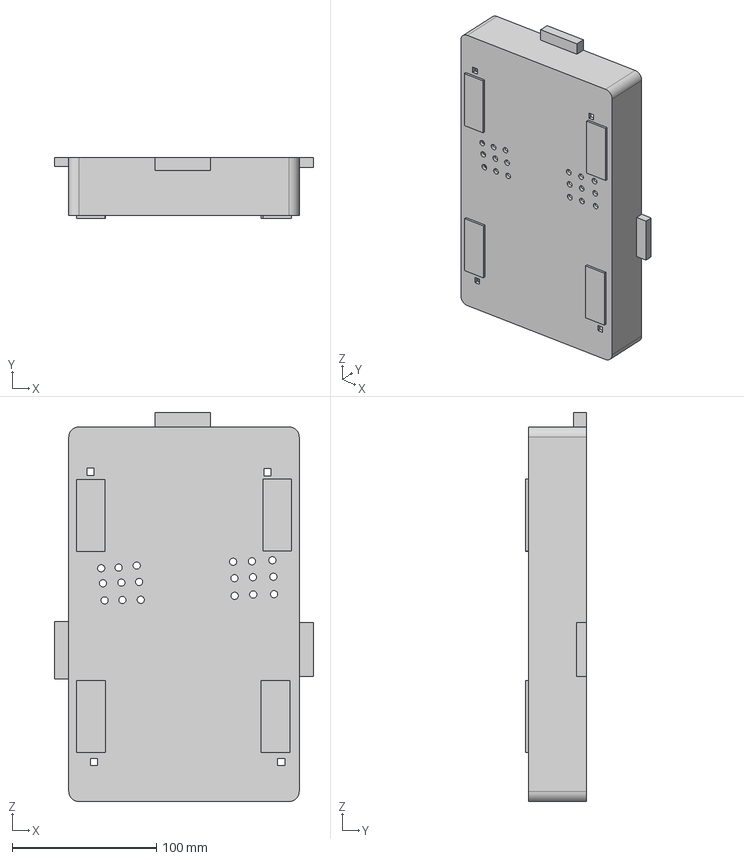
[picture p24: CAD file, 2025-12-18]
3D Models/robot_base.step
180.0 x 42.0 x 270.0 mm

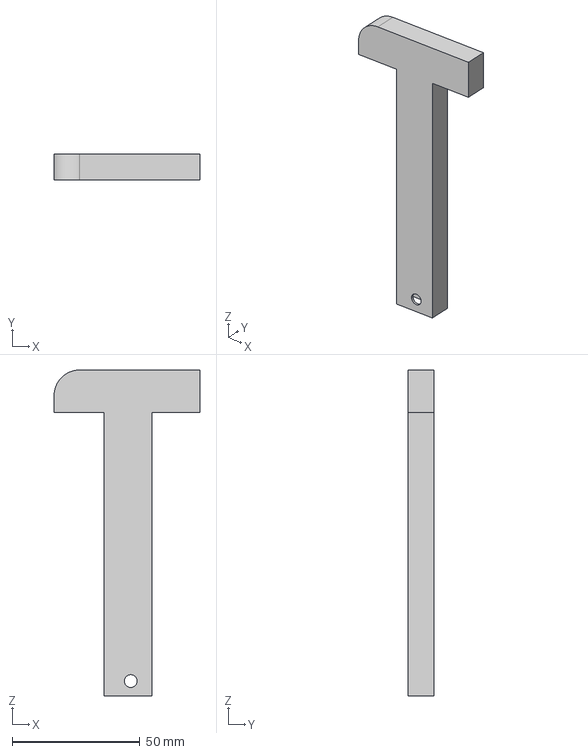
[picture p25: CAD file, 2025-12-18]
3D Models/robot_axe.step
57.2 x 10.0 x 127.8 mm

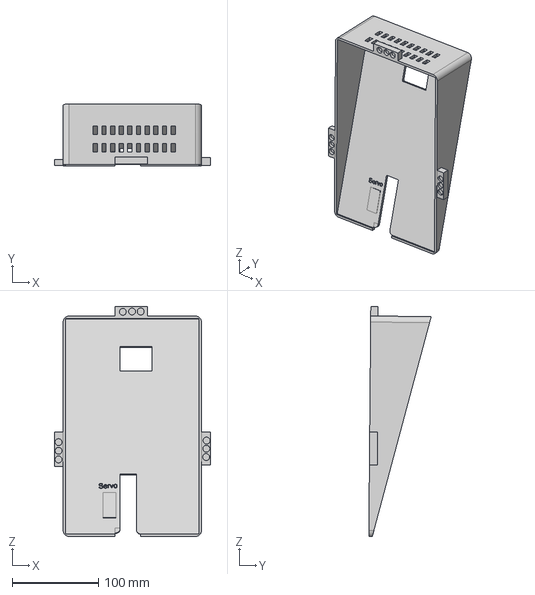
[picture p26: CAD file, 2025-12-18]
3D Models/robot_top.step
180.5 x 72.2 x 266.0 mm

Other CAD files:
3D Models/robot axe.f3d
3D Models/robot base.f3d
3D Models/robot remote CASE.f3z
3D Models/robot top.f3d
3D Models/robot with components.f3z

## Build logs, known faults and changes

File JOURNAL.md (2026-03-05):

<!--
  This journal is auto generated by Hack Club Blueprint.
-->

# 12/15/2025 - Planned out where the components will go in the robot  

_Time spent: 1.0h_  

I did a sketch of the setup for my custom battle robot project with the hardware placement. For example what will go on the breadboard, what battery devices I will need to power my components & what motor drivers I will need for my TT motors



# 12/18/2025 - Chassis design  

_Time spent: 3.0h_  

I finished designing my robot chassis for 3D printing - took many iterations.  I ended up with a single servo-driven axe weapon that rests on the slanted part of the chassis and swings forwards on command.

robot_design_image

I made holes in the base for the speaker audio, small indents for magnets so I can connect the bottom & top halves, and added text to the chassis for some extra personalisation.

robot_base_image

# 12/19/2025 - Importing components  

_Time spent: 1.0h_  

I imported 3D models of the electronic components into Fusion 360 so I can fully visualise their placements, applied textures to my robot and updated my github




# 12/26/2025 - Design re-review submission  

_Time spent: 3.0h_  

I sorted out my components, uploaded all of the cart screenshots to github & updated my BOM with my final amount. 



I also designed and finished my PCB for the remote, exported the gerber files & got a quote on JLCBPCB and uploaded the files & cart screenshot




I believe I'm ready for re-submission  

# 2/11/2026 - PCB design process update  

_Time spent: 0.5h_  

Added lots of more detail on the process behind designing the remote PCB for my robot. I talked about some issues I ran into as well as some design choices I made.

Repo preview:



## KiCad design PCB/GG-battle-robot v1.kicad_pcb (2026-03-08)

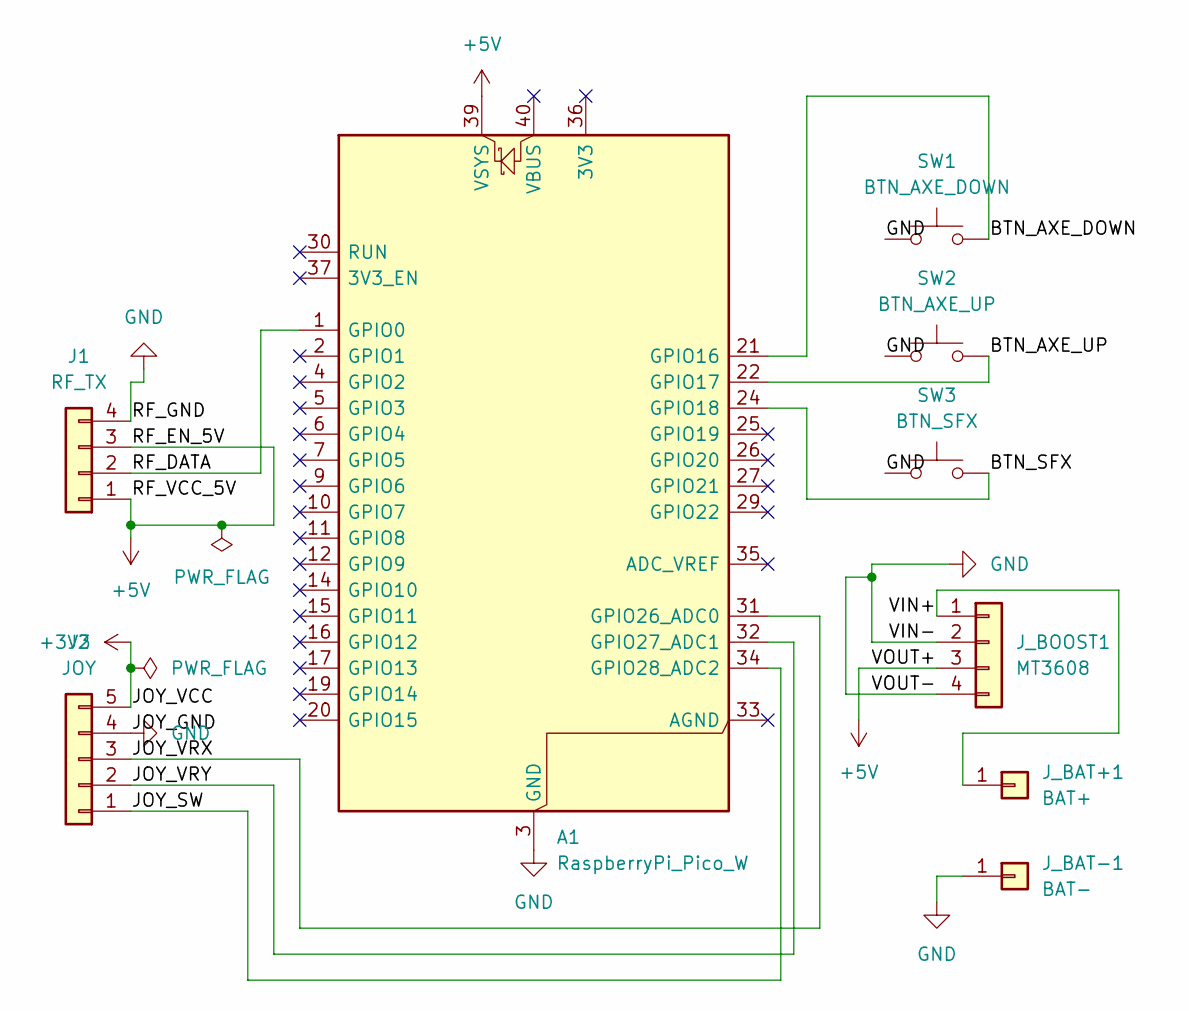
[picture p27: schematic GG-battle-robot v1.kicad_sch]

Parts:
A1: RaspberryPi_Pico_W; RaspberryPi_Pico_Common_THT
J1: RF_TX; PinHeader_1x04_P2.54mm_Vertical
J2: JOY; PinHeader_1x05_P2.54mm_Vertical
J_BAT+1: BAT+; SolderWirePad_1x01_SMD_5x10mm
J_BAT-1: BAT-; SolderWirePad_1x01_SMD_5x10mm
J_BOOST1: MT3608; PinHeader_1x04_P2.54mm_Vertical
SW1: BTN_AXE_DOWN; SW_Push_1TS009xxxx-xxxx-xxxx_6x6x5mm
SW2: BTN_AXE_UP; SW_Push_1TS009xxxx-xxxx-xxxx_6x6x5mm
SW3: BTN_SFX; SW_Push_1TS009xxxx-xxxx-xxxx_6x6x5mm

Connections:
+3V3: J2.5
+5V: A1.39 (VSYS), J1.1, J1.3, J_BOOST1.3
/BTN_AXE_DOWN: A1.21 (GPIO16), SW1.2
/BTN_AXE_UP: A1.22 (GPIO17), SW2.2
/BTN_SFX: A1.24 (GPIO18), SW3.2
/JOY_SW: A1.34 (GPIO28_ADC2), J2.1
/JOY_VRX: A1.31 (GPIO26_ADC0), J2.3
/JOY_VRY: A1.32 (GPIO27_ADC1), J2.2
/RF_DATA: A1.1 (GPIO0), J1.2
/VIN+: J_BAT+1.1, J_BOOST1.1
GND: A1.3 (GND), A1.8 (GND), A1.13 (GND), A1.18 (GND), A1.23 (GND), A1.28 (GND), A1.38 (GND), J1.4, J2.4, J_BAT-1.1, J_BOOST1.2, J_BOOST1.4, SW1.1, SW2.1, SW3.1

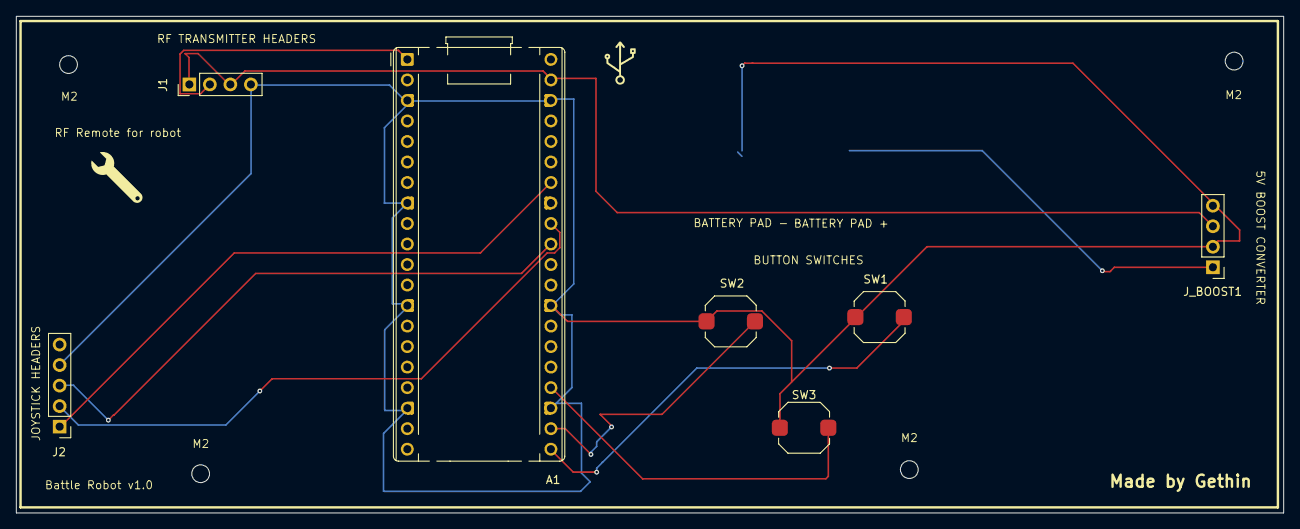
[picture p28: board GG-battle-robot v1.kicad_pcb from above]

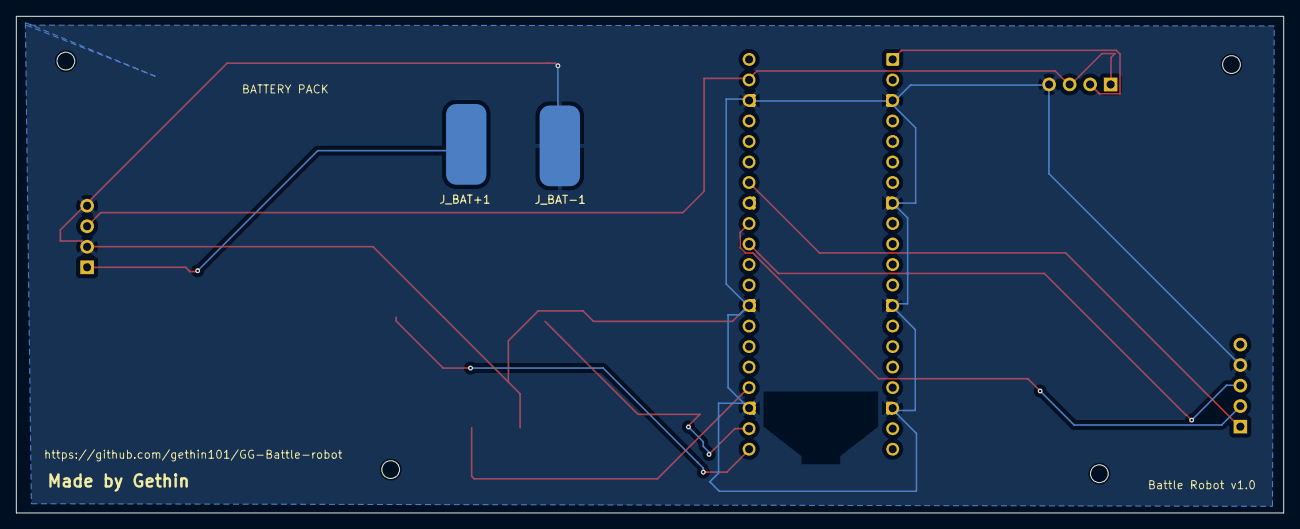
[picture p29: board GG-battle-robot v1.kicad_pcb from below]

Board: 2 copper layers, 156.9 x 61.5 mm, 9 parts (2 on the bottom side), 10 nets.

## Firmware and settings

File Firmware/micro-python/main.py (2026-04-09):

# -------------------------------------------------------------
# 4-WHEEL ROBOT CONTROLLED BY JOYSTICK (MICROPYTHON)
# Matching Gethin's exact wiring + joystick rotated 90° right
# -------------------------------------------------------------

from machine import Pin, PWM, ADC
import time

# -------------------------------------------------------------
# ANALOG JOYSTICK SETUP
# -------------------------------------------------------------
# VRx = GP26 (A0)
# VRy = GP27 (A1)
# Joystick rotated 90° → LEFT = forward, RIGHT = backward
# UP = turn right, DOWN = turn left

x_axis = ADC(26)   # VRx
y_axis = ADC(27)   # VRy

# Dead-zone (medium)
DEADZONE = 0.20

# -------------------------------------------------------------
# MOTOR DRIVER SETUP (L298N LEFT + RIGHT)
# -------------------------------------------------------------
# LEFT L298N pins
ENA_L = PWM(Pin(0))
IN1_L = Pin(1, Pin.OUT)
IN2_L = Pin(2, Pin.OUT)

ENB_L = PWM(Pin(3))
IN3_L = Pin(4, Pin.OUT)
IN4_L = Pin(5, Pin.OUT)

# RIGHT L298N pins
ENA_R = PWM(Pin(6))
IN1_R = Pin(7, Pin.OUT)
IN2_R = Pin(8, Pin.OUT)

ENB_R = PWM(Pin(9))
IN3_R = Pin(10, Pin.OUT)
IN4_R = Pin(11, Pin.OUT)

# Set PWM frequency
ENA_L.freq(1000)
ENB_L.freq(1000)
ENA_R.freq(1000)
ENB_R.freq(1000)

# -------------------------------------------------------------
# REVERSE OPTIONS (in case motors spin wrong)
# -------------------------------------------------------------
reverse_left = False
reverse_right = False

# -------------------------------------------------------------
# HELPER: SET MOTOR SPEED AND DIRECTION
# -------------------------------------------------------------
def drive_motor(pwmA, in1, in2, pwmB, in3, in4, speed, reverse=False):
    """
    Controls BOTH motors on one L298N board.
    speed = -1.0 to +1.0
    reverse = flips direction if motors wired backwards
    """

    if reverse:
        speed = -speed

    # Clamp speed
    if speed > 1: speed = 1
    if speed < -1: speed = -1

    # Convert speed to PWM duty (0–65535)
    duty = int(abs(speed) * 65535)

    if speed > 0:
        # Forward
        in1.value(1)
        in2.value(0)
        in3.value(1)
        in4.value(0)
    elif speed < 0:
        # Backward
        in1.value(0)
        in2.value(1)
        in3.value(0)
        in4.value(1)
    else:
        # Stop
        in1.value(0)
        in2.value(0)
        in3.value(0)
        in4.value(0)

    pwmA.duty_u16(duty)
    pwmB.duty_u16(duty)

# -------------------------------------------------------------
# MAIN LOOP
# -------------------------------------------------------------
while True:

    # Read joystick (0–65535)
    raw_x = x_axis.read_u16()
    raw_y = y_axis.read_u16()

    # Convert to -1.0 to +1.0
    x = (raw_x - 32768) / 32768
    y = (raw_y - 32768) / 32768

    # Apply dead-zone
    if abs(x) < DEADZONE: x = 0
    if abs(y) < DEADZONE: y = 0

    # ---------------------------------------------------------
    # MOVEMENT LOGIC (matching your rotated joystick)
    # ---------------------------------------------------------
    # LEFT  = forward
    # RIGHT = backward
    # UP    = turn right
    # DOWN  = turn left

    forward_back = -x      # LEFT = forward, RIGHT = backward
    turn = y               # UP = right turn, DOWN = left turn

    # Tank turn mixing
    left_speed = forward_back - turn
    right_speed = forward_back + turn

    # Clamp speeds
    left_speed = max(-1, min(1, left_speed))
    right_speed = max(-1, min(1, right_speed))

    # ---------------------------------------------------------
    # SEND SPEEDS TO MOTOR DRIVERS
    # ---------------------------------------------------------
    drive_motor(ENA_L, IN1_L, IN2_L, ENB_L, IN3_L, IN4_L, left_speed, reverse_left)
    drive_motor(ENA_R, IN1_R, IN2_R, ENB_R, IN3_R, IN4_R, right_speed, reverse_right)

    time.sleep(0.01)

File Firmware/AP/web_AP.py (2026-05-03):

import network
import socket
import time
from machine import Pin, PWM

# ============================
# MOTOR SETUP (your wiring)
# ============================

# LEFT SIDE L298N
L_ENA = PWM(Pin(0))
L_IN1 = Pin(1, Pin.OUT)
L_IN2 = Pin(2, Pin.OUT)
L_ENB = PWM(Pin(3))
L_IN3 = Pin(4, Pin.OUT)
L_IN4 = Pin(5, Pin.OUT)

# RIGHT SIDE L298N
R_ENA = PWM(Pin(6))
R_IN1 = Pin(7, Pin.OUT)
R_IN2 = Pin(8, Pin.OUT)
R_ENB = PWM(Pin(9))
R_IN3 = Pin(10, Pin.OUT)
R_IN4 = Pin(11, Pin.OUT)

# Set PWM frequency
for pwm in [L_ENA, L_ENB, R_ENA, R_ENB]:
    pwm.freq(1000)

# Default speed
speed = 30000

# ============================
# MOTOR CONTROL FUNCTIONS
# ============================

def stop_all():
    global speed
    for pin in [L_IN1, L_IN2, L_IN3, L_IN4, R_IN1, R_IN2, R_IN3, R_IN4]:
        pin.value(0)
    for pwm in [L_ENA, L_ENB, R_ENA, R_ENB]:
        pwm.duty_u16(0)

def forwards():
    L_IN1.value(1); L_IN2.value(0)
    L_IN3.value(1); L_IN4.value(0)
    R_IN1.value(1); R_IN2.value(0)
    R_IN3.value(1); R_IN4.value(0)
    L_ENA.duty_u16(speed); L_ENB.duty_u16(speed)
    R_ENA.duty_u16(speed); R_ENB.duty_u16(speed)

def backwards():
    L_IN1.value(0); L_IN2.value(1)
    L_IN3.value(0); L_IN4.value(1)
    R_IN1.value(0); R_IN2.value(1)
    R_IN3.value(0); R_IN4.value(1)
    L_ENA.duty_u16(speed); L_ENB.duty_u16(speed)
    R_ENA.duty_u16(speed); R_ENB.duty_u16(speed)

def left_turn():
    # Tank turn: left motors reverse, right motors forward
    L_IN1.value(0); L_IN2.value(1)
    L_IN3.value(0); L_IN4.value(1)
    R_IN1.value(1); R_IN2.value(0)
    R_IN3.value(1); R_IN4.value(0)
    L_ENA.duty_u16(speed); L_ENB.duty_u16(speed)
    R_ENA.duty_u16(speed); R_ENB.duty_u16(speed)

def right_turn():
    # Tank turn: right motors reverse, left motors forward
    L_IN1.value(1); L_IN2.value(0)
    L_IN3.value(1); L_IN4.value(0)
    R_IN1.value(0); R_IN2.value(1)
    R_IN3.value(0); R_IN4.value(1)
    L_ENA.duty_u16(speed); L_ENB.duty_u16(speed)
    R_ENA.duty_u16(speed); R_ENB.duty_u16(speed)

# Start stopped
stop_all()

# ============================
# WIFI ACCESS POINT SETUP
# ============================

ap = network.WLAN(network.AP_IF)
ap.config(essid="Gethin-Robot", password="combat123")
ap.active(True)

print("WiFi network created: Gethin-Robot")
print("Password: combat123")
print("Connect and go to: http://192.168.4.1")

# ============================
# HTML PAGE
# ============================

html = """<!DOCTYPE html>
<html>
<head>
<title>Gethin Robot</title>
<style>
body { text-align: center; font-family: Arial; }
button {
  width: 160px; height: 80px;
  font-size: 28px; margin: 10px;
}
select { font-size: 24px; padding: 10px; }
</style>
</head>
<body>
<h1>Gethin Robot Controller</h1>

<button onclick="location.href='/forwards'">FORWARDS</button><br>

<button onclick="location.href='/left'">LEFT</button>
<button onclick="location.href='/stop'">STOP</button>
<button onclick="location.href='/right'">RIGHT</button><br>

<button onclick="location.href='/backwards'">BACKWARDS</button><br><br>

Speed:
<select onchange="location.href='/speed?value=' + this.value">
  <option value="slow">Slow</option>
  <option value="medium" selected>Medium</option>
  <option value="fast">Fast</option>
</select>

</body>
</html>
"""

# ============================
# WEB SERVER + SAFETY STOP
# ============================

last_command_time = time.time()

def safety_check():
    global last_command_time
    if time.time() - last_command_time > 3:
        stop_all()

s = socket.socket()
s.bind(("0.0.0.0", 80))
s.listen(1)

while True:
    safety_check()
    conn, addr = s.accept()
    request = conn.recv(1024).decode()

    last_command_time = time.time()

    if "/forwards" in request:
        forwards()
    elif "/backwards" in request:
        backwards()
    elif "/left" in request:
        left_turn()
    elif "/right" in request:
        right_turn()
    elif "/stop" in request:
        stop_all()
    elif "/speed?value=slow" in request:
        speed = 15000
    elif "/speed?value=medium" in request:
        speed = 30000
    elif "/speed?value=fast" in request:
        speed = 45000

    conn.send("HTTP/1.1 200 OK\r\nContent-Type: text/html\r\n\r\n")
    conn.send(html)
    conn.close()

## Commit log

2025-12-26 Rename Screenshot 2025-12-26 092003.png to pcb.png
2026-02-11 Revise PCB design process details in README
    Updated the PCB section to provide a detailed overview of the design process, including component choices and design considerations.
2026-03-08 Update and rename Firmware/LED/led.py to Firmware/led.py
2026-03-08 Rename adafruit-circuitpython-raspberry_pi_pico2-en_GB-10.1.3 (1).uf2 to adafruit-circuitpython-raspberry_pi_pico2-en_GB-10.1.3.uf2
